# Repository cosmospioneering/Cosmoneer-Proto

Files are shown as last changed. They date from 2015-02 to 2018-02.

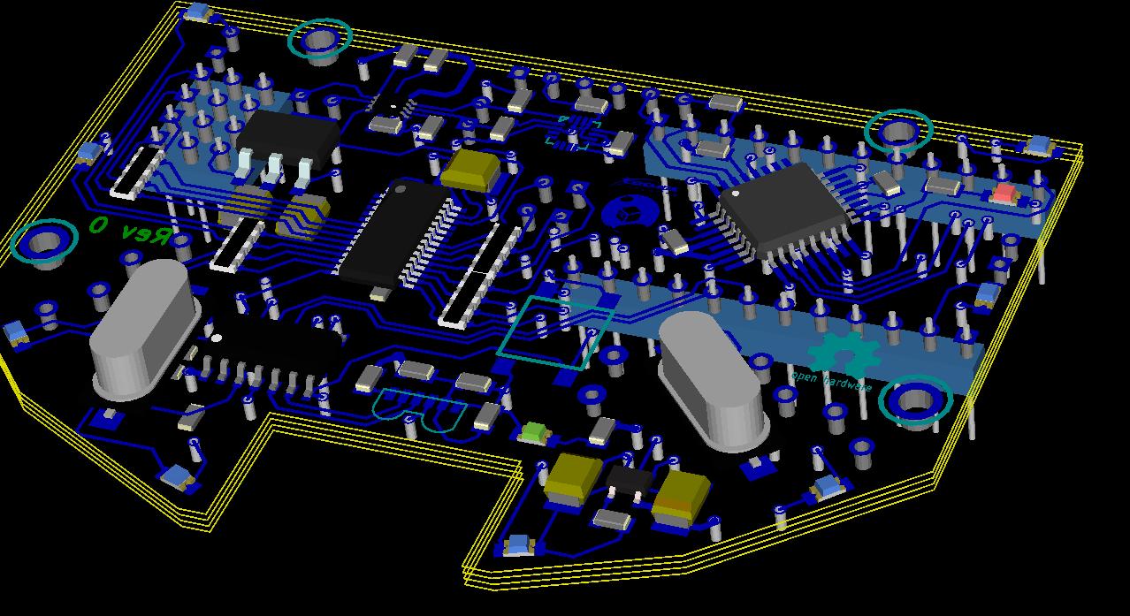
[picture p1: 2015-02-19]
CosmoneerJr_3D_Rev0.jpg

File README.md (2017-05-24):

#Cosmos Pioneering   -   Cosmoneer Proto#
==========================================

The Cosmoneer Proto is a single-degree of Freedom Spacecraft simulator.  This design is the main control board to manage the attitude in a single axis via PWM control through a server and gyro motor, commonly known as a Control Moment Gyro.

----------

# CONTENTS #

This repository contains source files for the Cosmoneer Proto.  Here is a table of contents for the repository.

- 3DModels: Rhino 3.0 models, with a sub folder containing Rhino output STL files
- Arduino: Arduino code in two folders, with additional required libraries contained in a separate zip file.
- Rev0-fab: Rev 0 PCB fabrication files (copper, mask, silk, drill, dwg)
- SpecSheets: Manufacturing spec sheets for components used on the Cosmoneer Proto circuit board
- fab: Rev 01 PCB fabrication files (copper, mask, silk, drill, dwg)
- boards: [KiCAD](http://www.kicad-pcb.org/display/KICAD/KiCad+EDA+Software+Suite) PCB board files (CosmoneerProto, SuperBurst & Serial IrDa)

# LICENSE #

*This project is open source hardware as defined by the* [Open Source Hardware (OSHW) Definition 1.0](http://freedomdefined.org/OSHW)
- Documentation under the following license:  [Creative Commons Attribution-ShareAlike 4.0 Unported License](http://creativecommons.org/licenses/by-sa/4.0/)
- Source code is under the following license:  [GNU General Public License, version 3 (GPL-3.0)](https://opensource.org/licenses/GPL-3.0)

[][1] [][3] [][5]

[1]: http://creativecommons.org/licenses/by-sa/4.0/
[2]: http://i.creativecommons.org/l/by-sa/4.0/88x31.png (Creative Commons Attribution-ShareAlike 4.0 Unported License.)

[3]: http://freedomdefined.org/OSHW
[4]: http://www.oshwa.org/wp-content/uploads/2014/03/oshw-logo-antipixel.png

[5]: https://opensource.org/licenses/GPL-3.0
[6]: https://www.gnu.org/graphics/gplv3-88x31.png

----------

# Disclaimer #

THE CONTENT OF THIS FOLDER IS PROVIDED "AS IS" AND "WITH ALL FAULTS". Cosmos Pioneering DISCLAIMS ALL OTHER WARRANTIES, EXPRESS OR IMPLIED, REGARDING PRODUCTS, INCLUDING BUT NOT LIMITED TO, ANY IMPLIED WARRANTIES OF MERCHANTABILITY OR FITNESS FOR A PARTICULAR PURPOSE.

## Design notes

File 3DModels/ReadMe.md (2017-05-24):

*3D Model File Notes*

1. The files are provided are used with Rhino 3.0.
  1. UOM is in millimeters
  2. STL files are generated using the following Rhino settings
    1. ?
    2. ?
2. STL files are provided for final component production.

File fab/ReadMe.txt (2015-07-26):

1> Copper weight & Layer thickness & material
     1oz copper.  Board thickness is .062"., FR4
 
2> Hole size tolerance and plating
     All holes are plated through, +/-003"(+/-0.08mm)

3> Soldermask tolerance & color
     .003"(0.075mm)  Color, blue
 
4> Plating & Leveling
     Hot Air Solder Level
 
5> Silkscreen side & color
     Top & Bottom silkscreen.  Color, White.
 
6> Dimensional size & tolerance
     70mm(2.756")  X  50mm(1.968"),  +/- 0.012"(0.3mm)
     Max radius on inside pcb corners is .070"
 
7> Electrical testing
     Electrical testing is not required

8> Inner layer isolated pads
    Isolated pads may be removed from inner layers.
 
9> Datecode & Mfg Marking
    Date Code and Mfg Code are not required.

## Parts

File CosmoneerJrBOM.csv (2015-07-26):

Id | Designator | Package | Quantity | Designation | Supplier and ref
1 | U3 | vishay_TFBS4711 | 1 | TFBS4711
2 | U1 | TQFP32 | 1 | ATMEGA328P-AU
3 | SW1 | SW_PUSH_SMD | 1 | SW_PUSH_SMALL
4 | U7 | SOT23-5 | 1 | MIC5205
5 | U8 | SOT223 | 1 | AMS1117
6 | U2 | so-14 | 1 | MCP2120-SL
7 | C15,C12,C11,C10,C17,C16,C3,C5 | SM0805 | 8 | 0.1uf
8 | R24,R22,R23,R20,R21,R7 | SM0805 | 6 | 10K
9 | R19,R18 | SM0805 | 2 | 1K
10 | C7,C14,C13,C6 | SM0805 | 4 | 22pf
11 | C8,C2,C4 | SM0805 | 3 | 4.7uf
12 | C9 | SM0805 | 1 | 0.22uf
13 | R17 | SM0805 | 1 | 0 Ohm
14 | R16 | SM0805 | 1 | 47 Ohm
15 | P1 | SIL-6 | 1 | .1in Header
16 | P2,P5,P4,P6 | SIL-2 | 4 | Header
17 | J17,J18 | SIL-12 | 2 | Header
18 | JP1,JP3,JP2,JP4,JP5 | S_JUMPER_3 | 5 | JUMPER3
19 | R25,R28 | r_CN2A4 | 2 | 220 Ohm
20 | R26,R27 | r_CN2A4 | 2 | 330 Ohm
21 | X2 | Q_49U3HMS | 1 | 16.000Mhz
22 | X1 | Q_49U3HMS | 1 | 7.3728Mhz
23 | J5,J1,J9,J13 | PIN_ARRAY_3X1 | 4 | Header
24 | PZ1 | piezo_spkr | 1 | PIEZO Speaker
25 | U4 | pca9306dcu | 1 | PCA9306
26 | D10,D9,D7,D8,D4,D6,D1,D2,D3,D5 | LED-0805 | 10 | LED
27 | U5 | HMC5883L_bigpads | 1 | HMC5883
28 | P3 | con-jst2-SM04B-SRSS-TB | 1 | SM04B-SRSS-TB
29 | C18,C1,C20,C21,C19 | c_tant_B | 5 | 10uf
30 | U9 | PCA9685 | 1 | PCA9685
31 | P7,P8 | SIL-2 | 2 | CONN_2
32 | 1PIN,1PIN,1PIN,1PIN | Mhole | 4 | P***
33 | PressFitPCB,PressFitPCB | PressFitPCB | 2 | VAL**
34 | G*** | Logo_silk_OSHW_6x6mm | 1 | LOGO
35 | VAL | LOGO | 1 | REF

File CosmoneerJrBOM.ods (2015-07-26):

Id | Designator | Package | Designation | Quantity | Supplier and ref
1 | U1 | TQFP32 | ATMEGA328P-AU | 1
2 | U2 | so-14 | MCP2120-SL | 1
3 | U3 | vishay_TFBS4711 | TFBS4711 | 1
4 | U4 | pca9306dcu | PCA9306 | 1
5 | U5 | HMC5883L_bigpads | HMC5883 | 1
6 | U7 | SOT23-5 | MIC5205 | 1
7 | U8 | SOT223 | AMS1117 | 1
8 | U9 | PCA9685 | PCA9685 | 1
9 | X1 | Q_49U3HMS | 7.3728Mhz | 1
10 | X2 | Q_49U3HMS | 16.000Mhz | 1
11 | SW1 | SW_PUSH_SMD | SW_PUSH_SMALL | 1
12 | PZ1 | piezo_spkr | PIEZO Speaker | 1
13 | D10,D9,D7,D8,D4,D6,D1,D2,D3,D5 | LED-0805 | LED | 10
14 | C15,C12,C11,C10,C17,C16,C3,C5 | SM0805 | 0.1uf | 8
15 | C9 | SM0805 | 0.22uf | 1
16 | C8,C2,C4 | SM0805 | 4.7uf | 3
17 | C18,C1,C20,C21,C19 | c_tant_B | 10uf | 5
18 | C7,C14,C13,C6 | SM0805 | 22pf | 4
19 | R17 | SM0805 | 0 Ohm | 1
20 | R16 | SM0805 | 47 Ohm | 1
21 | R19,R18 | SM0805 | 1K | 2
22 | R24,R22,R23,R20,R21,R7 | SM0805 | 10K | 6
23 | R26,R27 | r_CN2A4 | 330 Ohm | 2
24 | R25,R28 | r_CN2A4 | 220 Ohm | 2
25 | P1 | SIL-6 | .1in Header | 1
26 | P2,P5,P4,P6 | SIL-2 | Header | 4
27 | P7,P8 | SIL-2 | CONN_2 | 2
28 | J5,J1,J9,J13 | SIL-3 | Header | 4
29 | J17,J18 | SIL-12 | Header | 2
30 | P3 | con-jst2-SM04B-SRSS-TB | SM04B-SRSS-TB | 1
31 | PressFitPCB,PressFitPCB | PressFitPCB | VAL** | 2

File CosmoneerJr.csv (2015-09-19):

Id | Designator | Package | Quantity | Designation | Supplier and ref
1 | U3 | vishay_TFBS4711 | 1 | TFBS4711
2 | U1 | TQFP32 | 1 | ATMEGA328P-AU
3 | U7 | SOT23-5 | 1 | MIC5205
4 | U2 | so-14 | 1 | MCP2120-SL
5 | C15 | C12 | C17 | C16 | C3 | C5 | SM0805 | 6 | 0.1uf
6 | R24 | R20 | R21 | R7 | SM0805 | 4 | 10K
7 | R19 | R18 | SM0805 | 2 | 1K
8 | C7 | C6 | SM0805 | 2 | 27pf
9 | C2 | C4 | SM0805 | 2 | 4.7uf
10 | C14 | C13 | SM0805 | 2 | 15pf
11 | R17 | SM0805 | 1 | 0 Ohm
12 | R16 | SM0805 | 1 | 47 Ohm
13 | P1 | SIL-6 | 1 | .1 Header
14 | P2 | P4 | P6 | SIL-2 | 3 | Header
15 | J17 | J18 | SIL-12 | 2 | Header
16 | JP1 | JP3 | JP2 | JP4 | JP5 | S_JUMPER_3 | 5 | JUMPER3
17 | X2 | Q_49U3HMS | 1 | 16.000Mhz
18 | X1 | Q_49U3HMS | 1 | 7.3728Mhz
19 | J5 | J1 | J9 | J13 | PIN_ARRAY_3X1 | 4 | Header
20 | PZ1 | piezo_spkr | 1 | PIEZO Speaker
21 | D10 | D9 | D7 | D8 | D4 | D6 | D1 | D2 | D3 | D5 | LED-0805 | 10 | LED
22 | P3 | con-jst2-SM04B-SRSS-TB | 1 | SM04B-SRSS-TB
23 | C18 | C1 | C21 | C19 | C20 | c_tant_B | 5 | 10uf
24 | U9 | PCA9685 | 1 | PCA9685
25 | P7 | P8 | SIL-2 | 2 | CONN_2
30 | R26 | R25 | R27 | R28 | r_cat16-4 | 4 | 330 Ohm
31 | SW1 | smd_push2 | 1 | SW_PUSH_SMALL
32 | GY-271 | GY-271 | 1 | U10
33 | U8 | SOT223 | 1 | AMS1117
34 | F1 | SM1812 | 1 | FUSE
35 | D11 | DO-214AC(SMA) | 1 | 1N4001

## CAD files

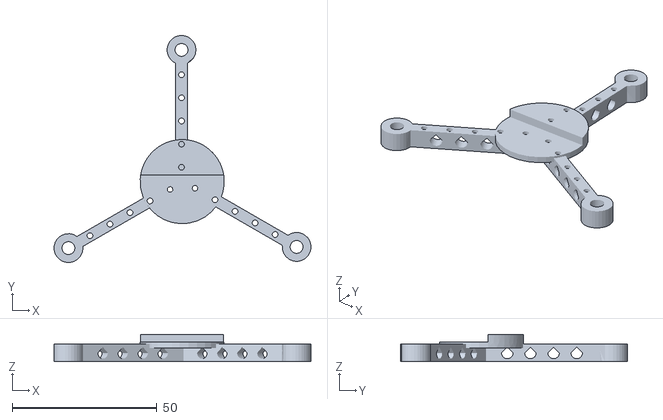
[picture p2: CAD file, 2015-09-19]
3DModels/3DPrintFiles/BalancerMain.stl
88.9 x 78.5 x 9.40

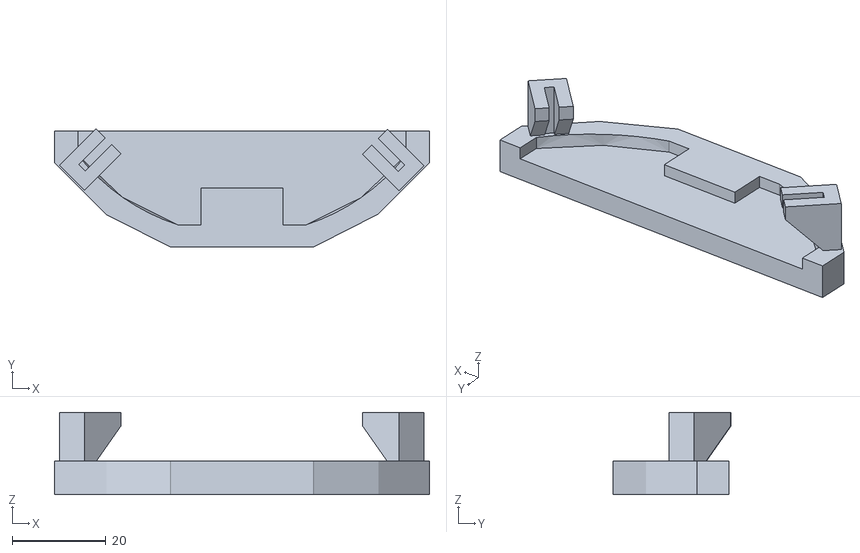
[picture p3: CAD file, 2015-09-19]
3DModels/3DPrintFiles/SupportJig_v2.stl
80.0 x 25.2 x 17.5

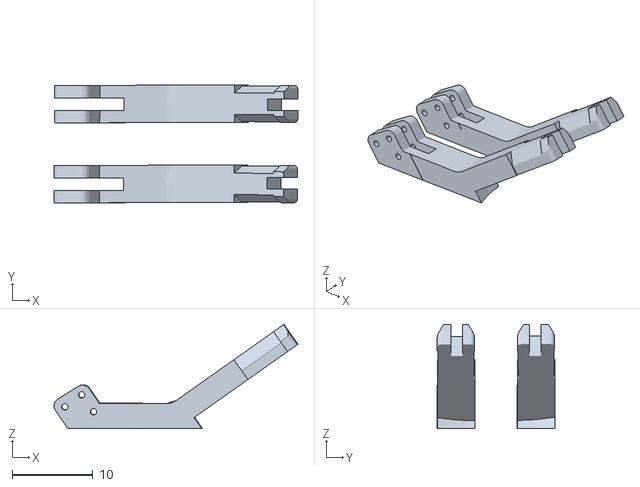
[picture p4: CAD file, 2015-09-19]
3DModels/3DPrintFiles/Legs_v2.stl
30.2 x 14.6 x 12.9

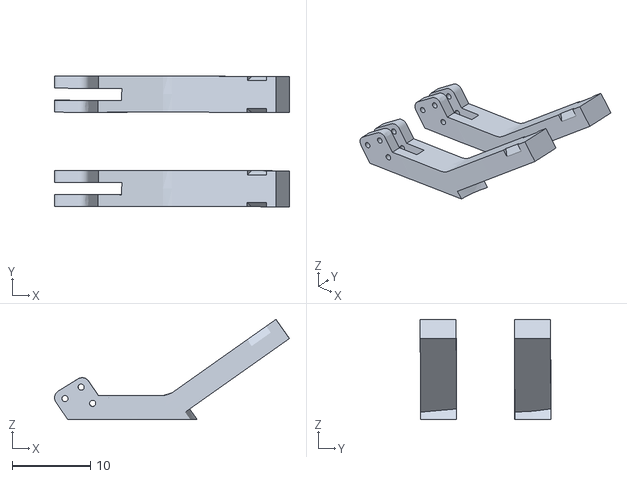
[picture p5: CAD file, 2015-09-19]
3DModels/3DPrintFiles/Legs.stl
30.1 x 16.8 x 12.9

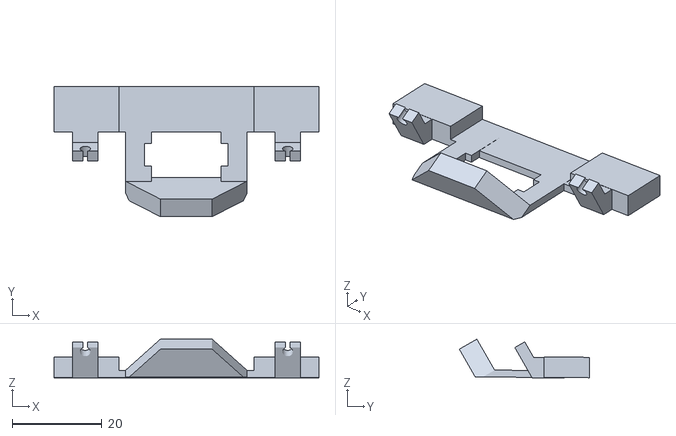
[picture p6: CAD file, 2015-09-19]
3DModels/3DPrintFiles/Evo_RearSupport_v3.stl
58.9 x 29.0 x 8.61

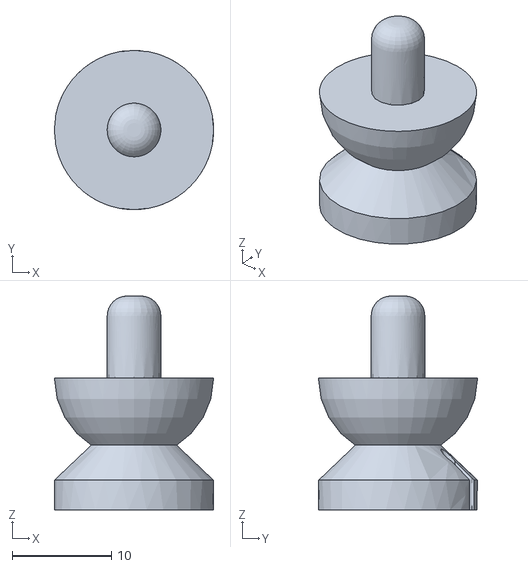
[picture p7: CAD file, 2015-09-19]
3DModels/3DPrintFiles/Spool_v6.stl
16.0 x 16.0 x 21.5

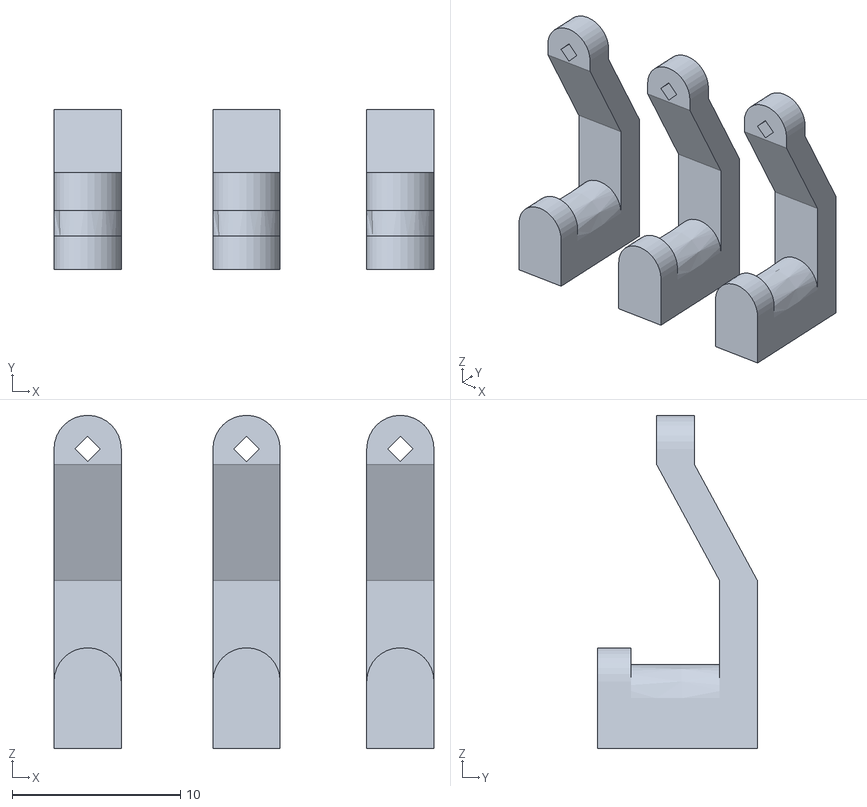
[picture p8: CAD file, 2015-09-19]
3DModels/3DPrintFiles/HangersX3_v2.stl
22.6 x 9.50 x 19.8

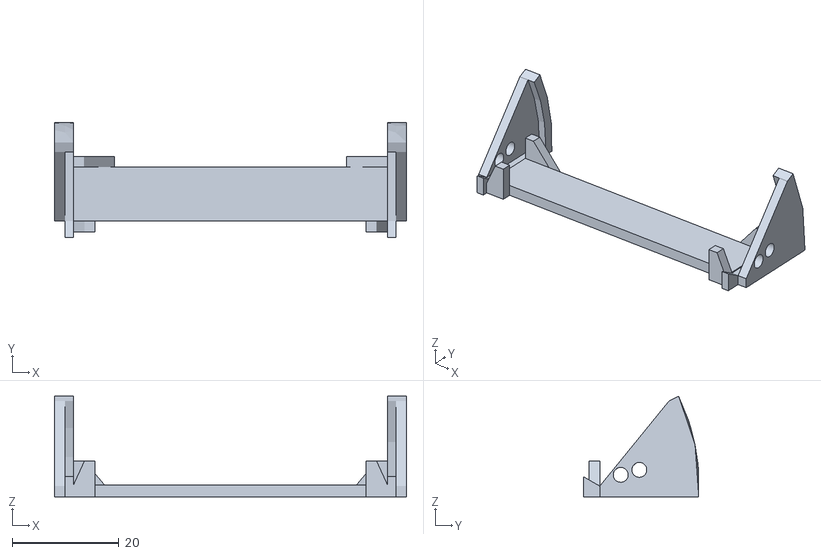
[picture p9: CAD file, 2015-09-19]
3DModels/3DPrintFiles/TopJig_v2.stl
66.0 x 21.7 x 18.9

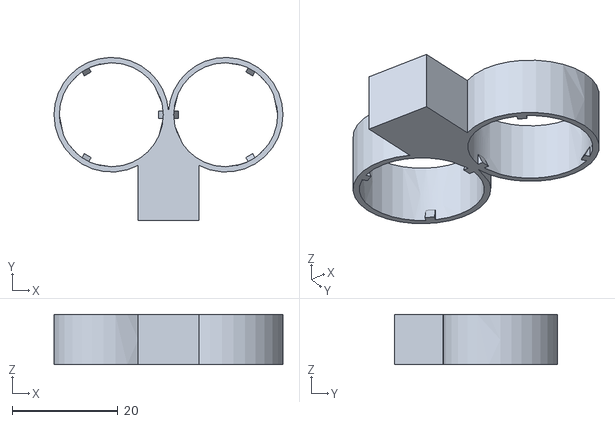
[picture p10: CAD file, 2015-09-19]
3DModels/3DPrintFiles/Counterweight_v1.stl
43.4 x 30.9 x 9.50

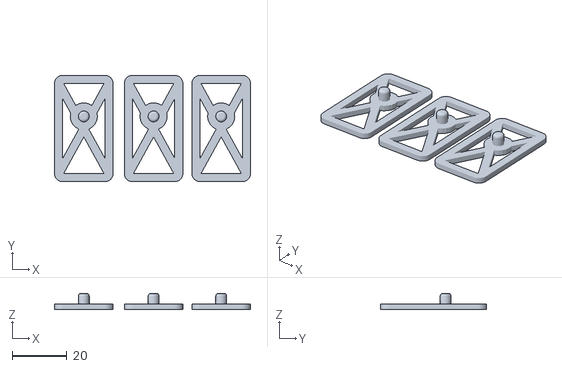
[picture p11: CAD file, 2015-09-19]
3DModels/3DPrintFiles/BalancerFeet.stl
71.9 x 39.0 x 6.00

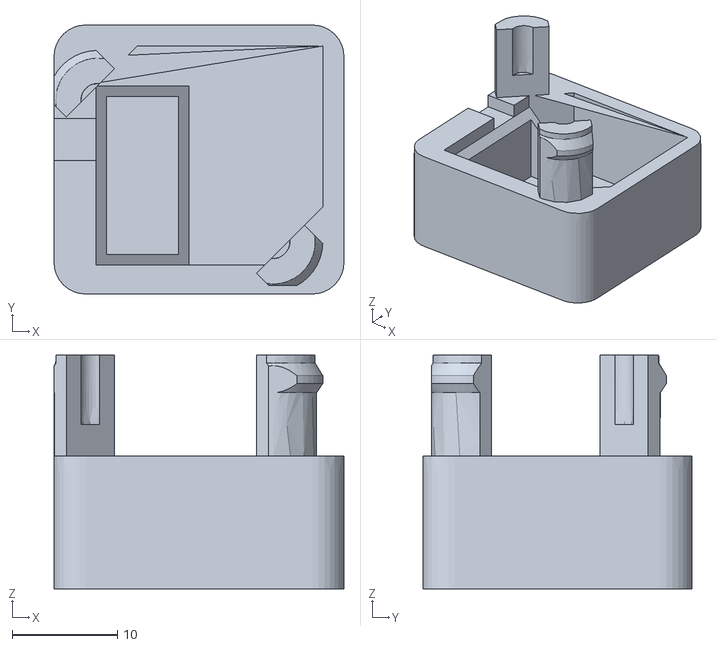
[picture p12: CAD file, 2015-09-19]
3DModels/3DPrintFiles/ChargeCover_v4.stl
27.5 x 25.6 x 22.2

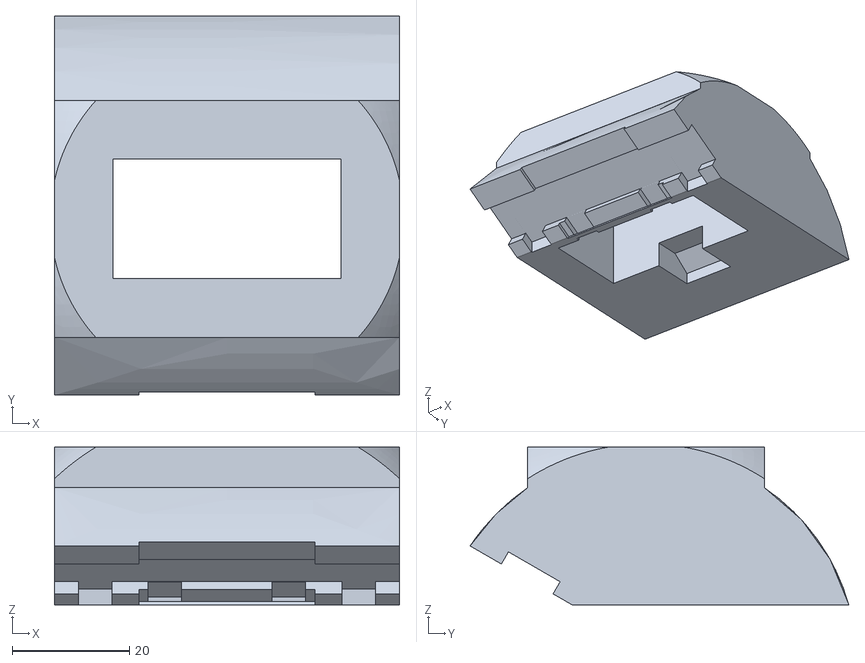
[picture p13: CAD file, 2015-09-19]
3DModels/3DPrintFiles/SeatingTool.stl
58.9 x 64.7 x 26.9

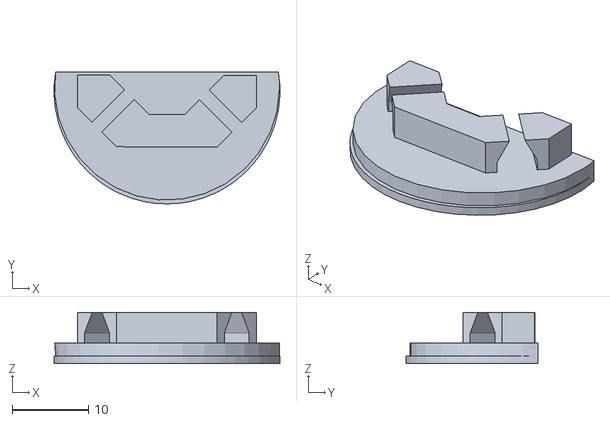
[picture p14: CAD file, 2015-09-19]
3DModels/3DPrintFiles/CoilPlate_v2.stl
29.6 x 17.3 x 6.70

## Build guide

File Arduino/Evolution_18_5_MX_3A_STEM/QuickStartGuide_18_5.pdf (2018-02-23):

## Your Cosmoneer is running open source test code!

To modify our code,
download and install
Arduino v1.6.10. Then,
install the library zip files in the project subfolder.

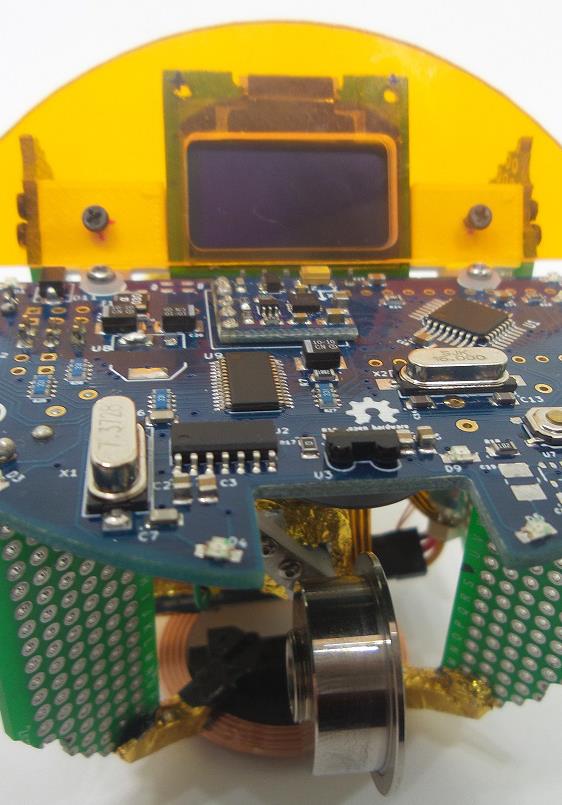
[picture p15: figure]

Your loaded version is:
Evolution_18_5_MX-3A_STEM

https://git.io/vA2jV

Replacement 3D parts:

https://www.thingiverse.
com/thing:2159548 (https://www.thingiverse.com/thing:2159548)

https://www.thingiverse.
com/thing:2154587 (https://www.thingiverse.com/thing:2154587)

You’ll find plenty of our Cosmoneer resources and useful information by visiting any one of the links below.

## Manuals & Documentation

http://cosmospioneering.com/manuals-and-docs/ (http://cosmospioneering.com/manuals-and-docs/)

## Cosmoneer User Community

http://cosmospioneering.com/community/

## GitHub Repository

https://github.com/cosmospioneering/Cosmoneer-Proto (https://github.com/cosmospioneering/Cosmoneer-Proto)

## Detailed Assembly Guide:

http://www.instructables.com/id/Cosmoneer-Proto/ (http://www.instructables.com/id/Cosmoneer-Proto/)

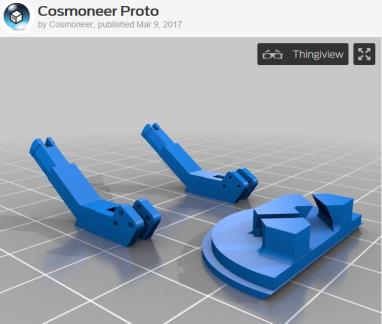
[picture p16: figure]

## Contact Us

PO Box 591 Damascus, MD 20872 240-200-4189
Cosmoneer@cosmospioneering.com http://www.cosmospioneering.com
- @Cosmoneer
- facebook.com/cosmos.pioneering

## Quick Start Guide

Congratulations on your purchase!

Your adventure in space
exploration begins here. Please take a moment to familiarize yourself with your personal desktop spacecraft.

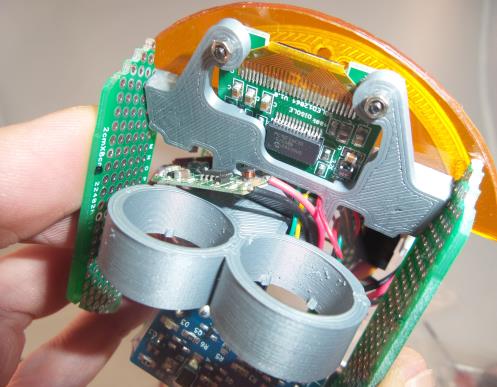
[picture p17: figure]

## Unboxing & Setup

Before removing your Cosmoneer from the box, please ensure you have a location available where your Cosmoneer will be level, safe & sound, and have an outlet within 3ft.

Find a smooth surface where you can lay out the parts. Carefully pull the Cosmoneer and its support
components from the box and place them on your surface.

Pull the hook and spool
from the Ziploc bag and
insert the spool into the
top of the hanger. Thread the string so it spills over the
edge towards the
center of the coil.

Place the unit in your
chosen location and
connect the power. It
is normal for the coil to
get warm during use.

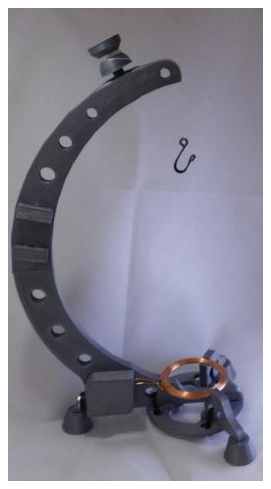
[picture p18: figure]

We recommend you use an adhesive or no-slip surface to prevent damage to your Cosmoneer from a fall during normal operation.

With the Cosmoneer in hand, place an equal number of the provided pennies into each of the wells in the rear of the Cosmoneer (shown above.)

## To sphere or not to sphere?

Your Cosmoneer can operate from within the 100mm sphere, or it can run while exposed to the harsh environment you have chosen. The sphere will smooth the Cosmoneers’ operations a bit, due to added mass.

If your Cosmoneer is experiencing high rotational speed, use the sphere. If you need more power, remove the sphere and suspend from the internal arch in front of the display which will allow you to reduce the coil airgap.

Using the sphere
Correctly placing the Cosmoneer into the sphere has been simplified via rubber guides. To start, grasp the sphere half containing the guides, open side facing up.

The guide opposite the hanger loop is where the coil of the Cosmoneer will sit. With the Cosmoneer in your other hand, lay it on its back and align the coil hanger as shown. Be sure to align the
dash panel
against the guides
at the opposite
end of the sphere.

With everything

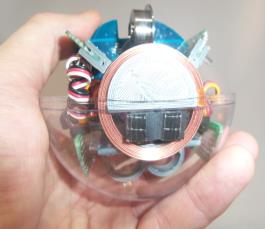
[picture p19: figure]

aligned, join the
sphere halves
together, making
sure the pennies
don’t fall out of
the holder.

## Launch!

To launch, simply place the craft onto the hook and adjust the spool so the craft is suspended just above the coil. Your Cosmoneer will power up in about ten seconds. Have fun!

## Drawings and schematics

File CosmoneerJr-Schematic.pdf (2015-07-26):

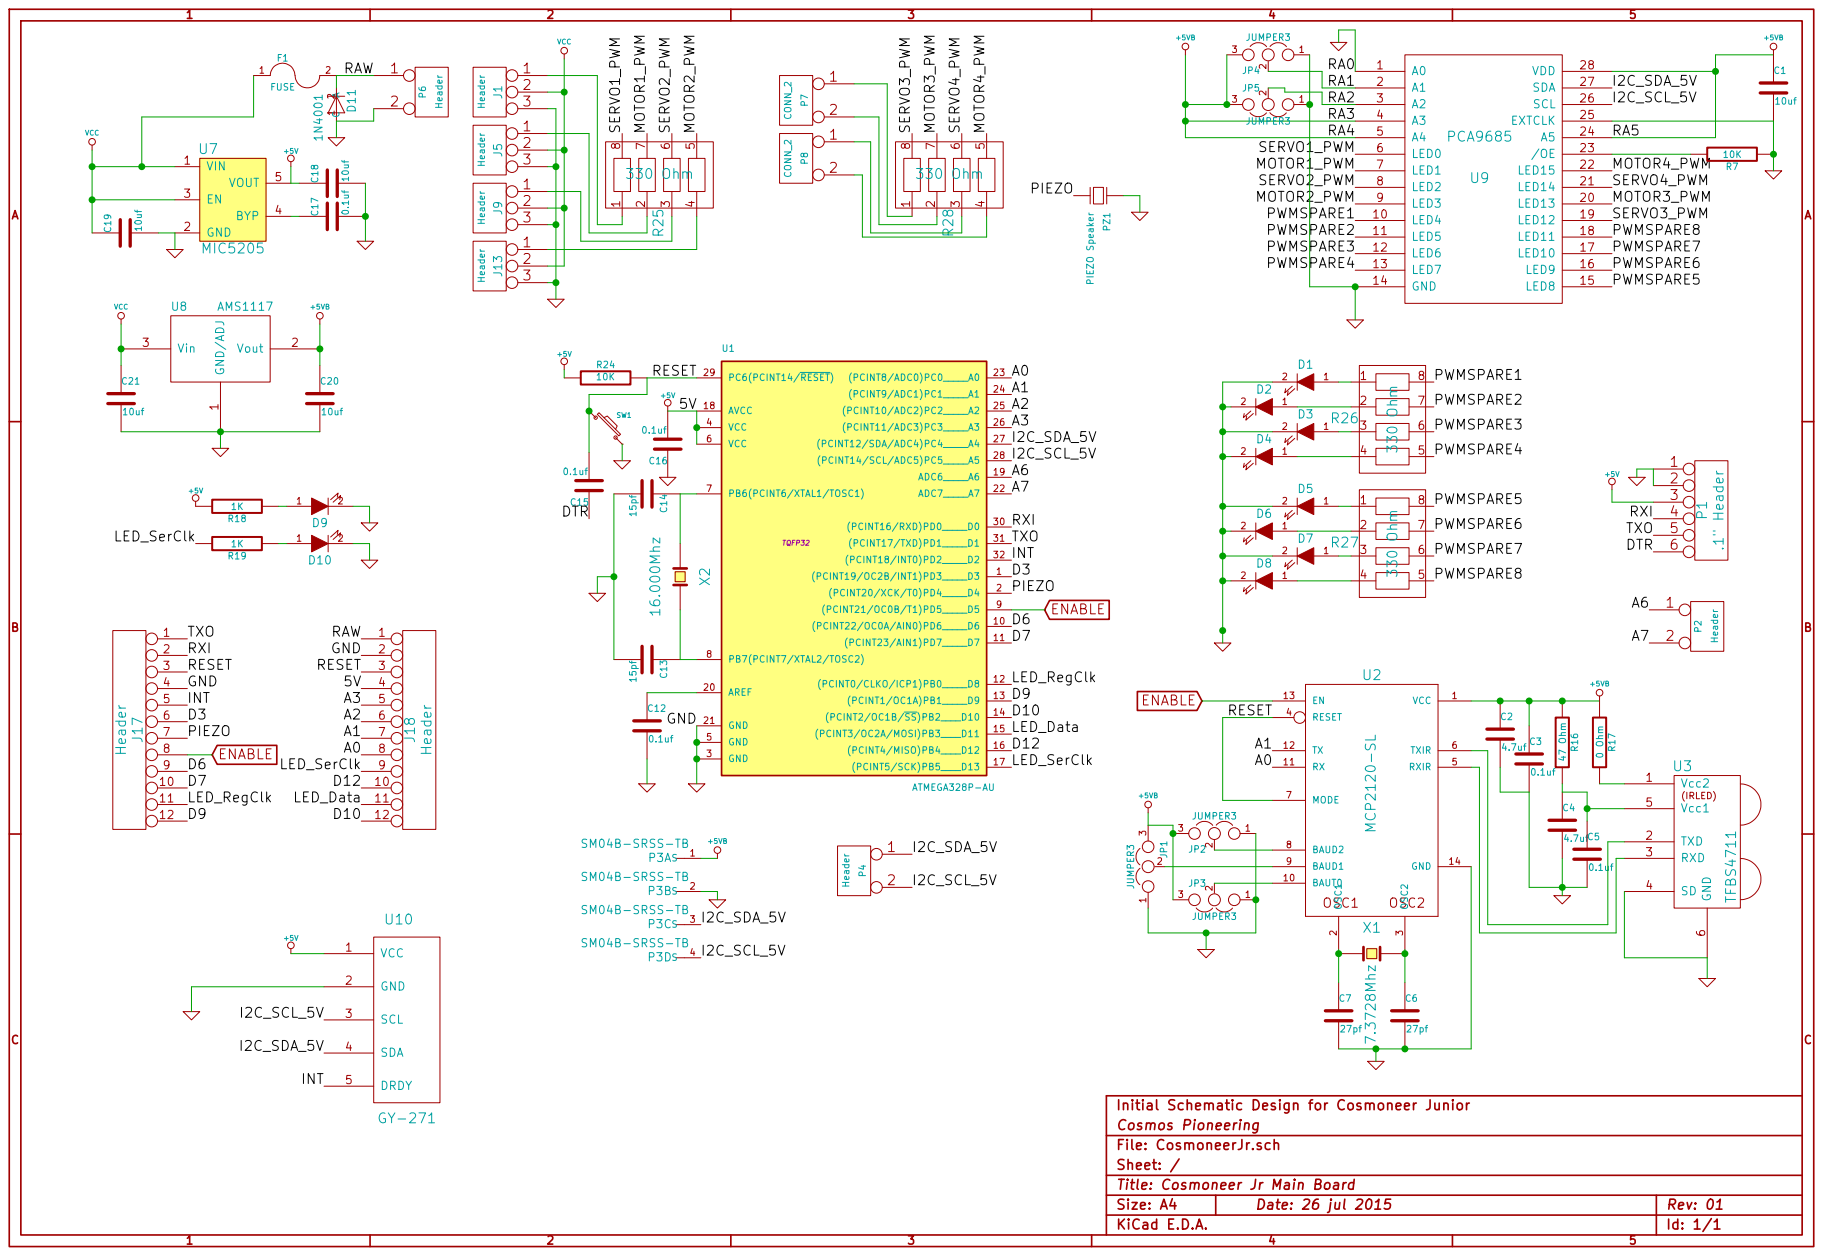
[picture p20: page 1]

3 RESET 4 RXIR 5 TXIR 6 MODE 7 BAUD2 8 BAUD1 9 BAUT0 10 RX 11 TX 12 EN 13 GND 14 U2MCP2120-SL ENABLE

Initial Schematic Design for Cosmoneer Junior
Id: 1/1 Title: Cosmoneer Jr Main Board File: CosmoneerJr.sch Sheet: / Cosmos Pioneering

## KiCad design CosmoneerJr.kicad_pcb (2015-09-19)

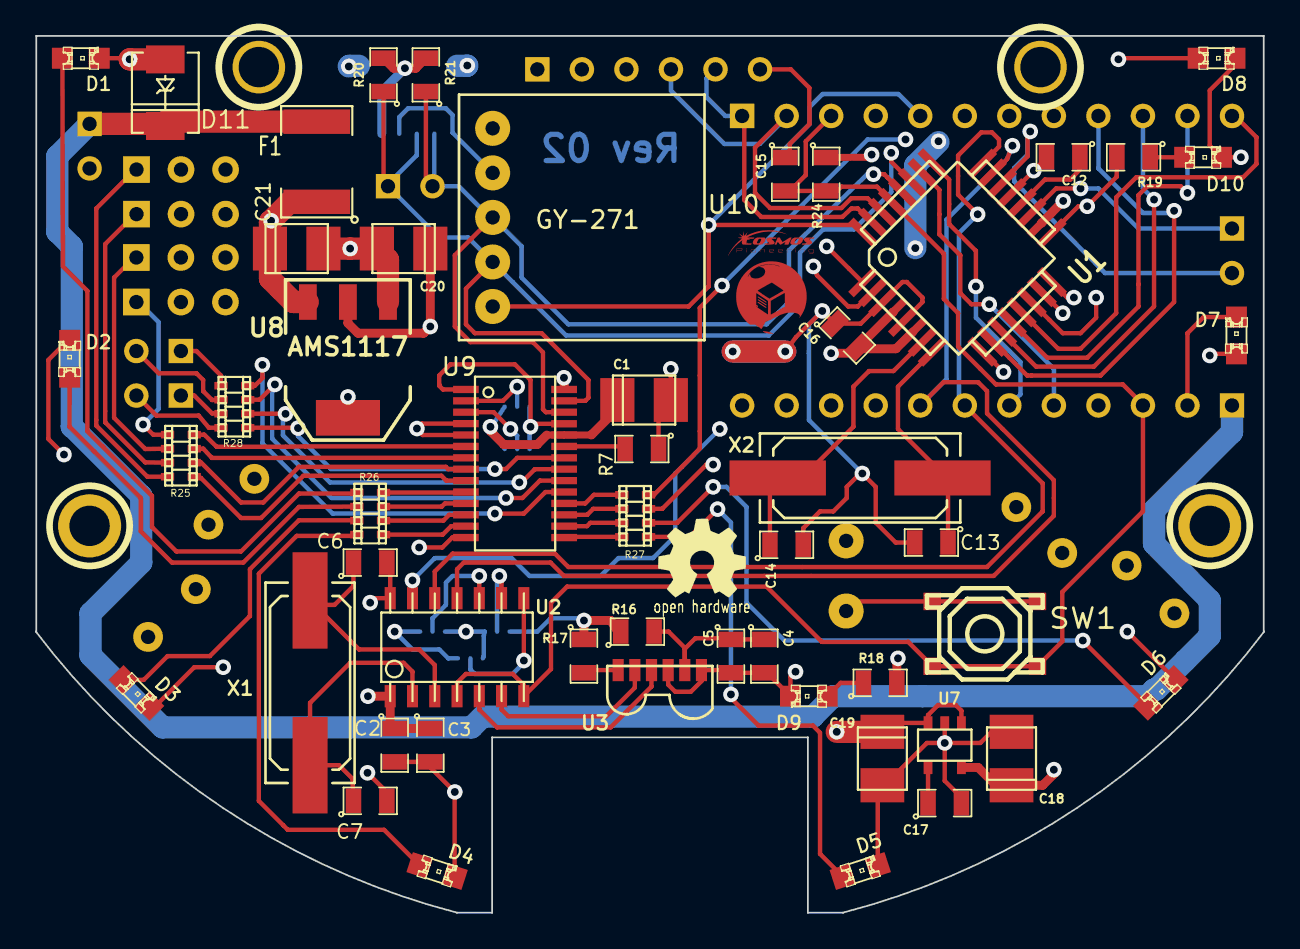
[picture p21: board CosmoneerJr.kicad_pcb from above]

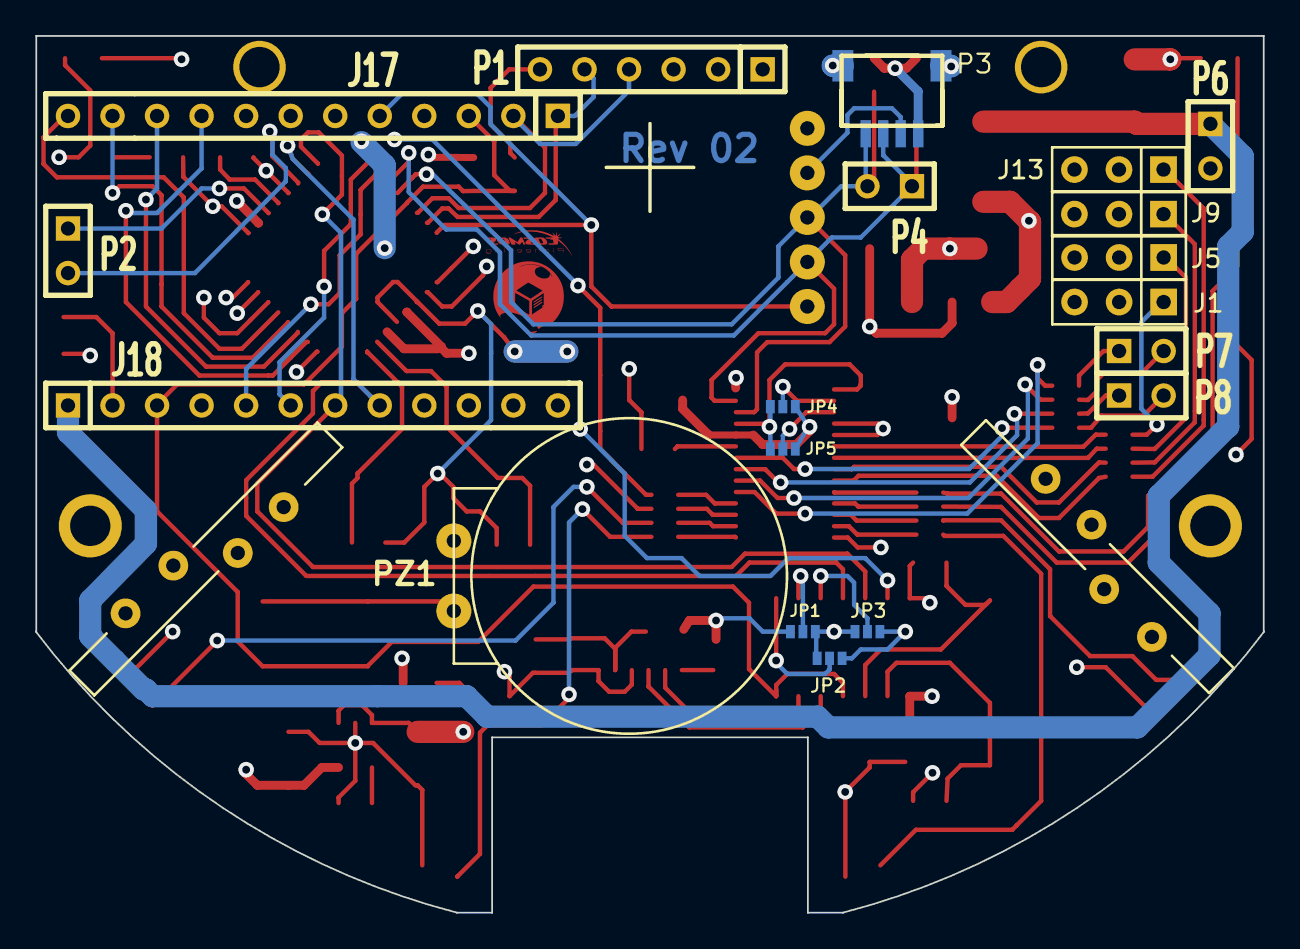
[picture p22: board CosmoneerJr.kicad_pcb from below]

Board: 4 copper layers, 70.0 x 50.0 mm, 77 parts (21 on the bottom side), 78 nets.

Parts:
1PIN, 1PIN#2, 1PIN#3, 1PIN#4: P***; Mhole
C1, C18, C19, C20, C21: 10uf; c_tant_B
C2, C4: 4.7uf; SM0805
C3, C5, C12, C15, C16, C17: 0.1uf; SM0805
C6, C7: 27pf; SM0805
C13, C14: 15pf; SM0805
D1, D2, D3, D4, D5, D6, D7, D8, D9, D10: LED; LED-0805
D11: 1N4001; DO-214AC(SMA)
F1: FUSE; SM1812
GY-271: U10; GY-271
J1, J5, J9, J13: Header; PIN_ARRAY_3X1
J17, J18: Header; SIL-12
JP1, JP2, JP3, JP4, JP5: JUMPER3; S_JUMPER_3
P1: .1" Header; SIL-6
P2, P4, P6: Header; SIL-2
P3: SM04B-SRSS-TB; con-jst2-SM04B-SRSS-TB
P7, P8: CONN_2; SIL-2
PZ1: PIEZO Speaker; piezo_spkr
PressFitPCB: VAL**; PressFitPCB
PressFitPCB#2: VAL**; PressFitPCB
R7, R20, R21, R24: 10K; SM0805
R16: 47 Ohm; SM0805
R17: 0 Ohm; SM0805
R18, R19: 1K; SM0805
R25, R26, R27, R28: 330 Ohm; r_cat16-4
SW1: SW_PUSH_SMALL; smd_push2
U1: ATMEGA328P-AU; TQFP32
U2: MCP2120-SL; so-14
U3: TFBS4711; vishay_TFBS4711
U7: MIC5205; SOT23-5
U8: AMS1117; SOT223
U9: PCA9685
VAL: REF; LOGO
X1: 7.3728Mhz; Q_49U3HMS
X2: 16.000Mhz; Q_49U3HMS

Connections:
+5V: C1.1, C2.1, C3.1, C16.2, C18.1, C20.1, GY-271.1, J18.4, JP1.3, JP2.3, JP3.3, JP4.3, JP5.3, P1.3, P3.1, R16.1, R17.1, R18.2, R20.2, R21.2, R24.1, U1.4, U1.6, U1.18, U2.1, U7.5, U8.2, U8.4, U9.4, U9.5, U9.24, U9.28
/A0: J18.8, U1.23, U2.11
/A1: J18.7, U1.24, U2.12
/A2: J18.6, U1.25
/A3: J18.5, U1.26
/A6: P2.1, U1.19
/A7: P2.2, U1.22
/D3: J17.6, U1.1
/D6: J17.9, U1.10
/D7: J17.10, U1.11
/D9: J17.12, U1.13
/D10: J18.12, U1.14
/D12: J18.10, U1.16
/DTR: C15.1, P1.6
/I2C_SCL_5V: GY-271.3, P3.4, P4.2, R21.1, U1.28, U9.26
/I2C_SDA_5V: GY-271.4, P3.3, P4.1, R20.1, U1.27, U9.27
/INT: GY-271.5, J17.5, U1.32
/LED_Data: J18.11, U1.15
/LED_RegClk: J17.11, U1.12
/LED_SerClk: J18.9, R19.2, U1.17
/MOTOR1_PWM: R25.7, U9.7
/MOTOR2_PWM: R25.5, U9.9
/MOTOR3_PWM: R28.7, U9.20
/MOTOR4_PWM: R28.5, U9.22
/PIEZO: J17.7, PZ1.2, U1.2
/PWMSPARE1: R26.8, U9.10
/PWMSPARE2: R26.7, U9.11
/PWMSPARE3: R26.6, U9.12
/PWMSPARE4: R26.5, U9.13
/PWMSPARE5: R27.8, U9.15
/PWMSPARE6: R27.7, U9.16
/PWMSPARE7: R27.6, U9.17
/PWMSPARE8: R27.5, U9.18
/RA1: JP4.2, U9.2
/RA2: JP5.2, U9.3
/RAW: D11.2, F1.2, J18.1, P6.1
/RESET: C15.2, J17.3, J18.3, R24.2, SW1.1, SW1.4, U1.29, U2.4, U2.7
/RXI: J17.2, P1.4, U1.30
/SERVO1_PWM: R25.8, U9.6
/SERVO2_PWM: R25.6, U9.8
/SERVO3_PWM: R28.8, U9.19
/SERVO4_PWM: R28.6, U9.21
/TXO: J17.1, P1.5, U1.31
ENABLE: J17.8, U1.9, U2.13
GND: 1PIN#3.1, C1.2, C2.2, C3.2, C4.2, C5.2, C6.2, C7.2, C12.2, C13.2, C14.2, C16.1, C17.2, C18.2, C19.2, C20.2, C21.2, D1.2, D2.2, D3.2, D4.2, D5.2, D6.2, D7.2, D8.2, D9.2, D10.2, D11.1, GY-271.2, J1.3, J5.3, J9.3, J13.3, J17.4, J18.2, JP1.1, JP2.1, JP3.1, JP4.1, JP5.1, P1.1, P1.2, P3.2, P3.FIT@, P6.2, PZ1.1, R7.1, SW1.2, SW1.3, U1.3, U1.5, U1.21, U2.14, U3.4, U3.6, U7.2, U8.1, U9.1, U9.14, U9.25
unnamed: JP3.2, U2.10
unnamed: C12.1, U1.20
unnamed: U2.5, U3.3
unnamed: U2.6, U3.2
unnamed: C4.1, C5.1, R16.2, U3.5
unnamed: JP2.2, U2.8
unnamed: JP1.2, U2.9
unnamed: D10.1, R19.1
unnamed: C17.1, U7.4
unnamed: D9.1, R18.1
unnamed: C14.1, U1.7, X2.1
unnamed: C13.1, U1.8, X2.2
unnamed: R7.2, U9.23
unnamed: P8.1, R28.3
unnamed: P8.2, R28.4
unnamed: P7.1, R28.1
unnamed: P7.2, R28.2
unnamed: J13.1, R25.4
unnamed: J1.1, R25.1
unnamed: J5.1, R25.2
unnamed: J9.1, R25.3
unnamed: D6.1, R27.2
unnamed: D1.1, R26.1
unnamed: D2.1, R26.2
unnamed: D3.1, R26.3
unnamed: D4.1, R26.4
unnamed: D5.1, R27.1
unnamed: D7.1, R27.3
unnamed: D8.1, R27.4
unnamed: R17.2, U3.1
unnamed: C7.1, U2.2, X1.1
unnamed: C6.1, U2.3, X1.2
VCC: C19.1, C21.1, F1.1, J1.2, J5.2, J9.2, J13.2, U7.1, U7.3, U8.3

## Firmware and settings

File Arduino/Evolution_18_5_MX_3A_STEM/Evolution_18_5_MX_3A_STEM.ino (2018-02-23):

#include <MPU6050_6Axis_MotionApps20.h>


//----------------------------------------------
//    Wire Library   - I2C Bus Communications
//----------------------------------------------
#include <Wire.h>
//#include <i2cdetect.h>
//    This is required for...
//    Magnetometer
//    PWM Controller  
//    OLED Display (optional)
//
//
//Thanks, Adafruit for the awesome Servo Driver Library!
#include <Adafruit_PWMServoDriver.h>
//
//OLED Display interface
#define _Digole_Serial_I2C_  //To tell compiler compile the special communication only, 
#include <DigoleSerial.h>
//
//Compass interface & calibration code
#include "compass.h"
#include <MPU6050.h>


#include <string.h>



//----------------------------------------------
//    SoftSerial Library   - For Serial IrDa
//----------------------------------------------
#include <SoftwareSerial.h>



//----------------------------------------------
//    EEProm Library   - For Compass Cal Vals
//----------------------------------------------
#include <EEPROM.h>



//This is what is required for the timer event support
//----------------------------------------------
//    Timer Library   - Timed Events
//----------------------------------------------
#include "Timer.h"



#include "I2Cdev.h"
// class default I2C address is 0x68
// specific I2C addresses may be passed as a parameter here
// AD0 low = 0x68 (default for SparkFun breakout and InvenSense evaluation board)
// AD0 high = 0x69
MPU6050 mpu;




const uint8_t startscreenIV[1024] PROGMEM={
0,0,0,0,0,0,0,0,0,0,0,0,0,0,0,0
,0,0,0,0,0,0,0,0,0,0,0,0,0,0,0,0
,0,0,0,0,0,0,0,0,0,0,0,0,0,0,0,0
,0,0,0,0,0,0,0,0,0,0,0,0,0,0,0,0
,0,0,0,0,0,0,0,0,0,0,0,0,0,0,0,0
,0,0,0,0,0,0,0,0,0,0,0,0,0,0,0,0
,0,0,0,0,0,0,0,0,0,0,0,0,0,0,0,0
,0,0,0,0,0,0,0,0,0,0,0,0,0,0,0,0
,0,0,0,0,0,0,0,0,0,0,0,0,0,0,0,0
,0,0,0,0,0,0,0,0,0,0,0,0,0,0,0,0
,0,0,0,0,0,0,0,0,0,0,0,0,0,0,0,0
,0,0,0,0,0,0,0,0,0,0,0,0,0,0,0,0
,0,0,0,0,0,0,0,0,0,0,0,0,0,0,0,0
,0,0,0,0,0,0,0,0,0,0,0,0,0,0,0,0
,0,0,0,0,0,0,0,0,0,0,0,0,0,0,0,0
,0,0,0,0,0,0,0,0,0,0,0,0,0,0,0,0
,255,0,0,0,0,0,0,0,0,0,0,0,0,0,0,0
,128,0,0,0,0,0,0,0,0,0,0,0,0,0,0,0
,128,2,2,4,0,16,63,128,127,0,128,128,126,1,0,1
,255,2,2,4,0,16,0,64,0,128,128,128,195,1,0,1
,129,2,2,4,0,16,31,224,63,192,128,128,129,1,0,1
,129,2,2,4,0,16,48,32,96,64,128,128,129,1,1,255
,129,2,2,4,0,48,32,32,64,64,128,128,129,1,3,1
,255,3,252,4,15,224,63,192,127,128,255,0,255,1,2,1
,0,0,0,0,0,0,0,0,0,0,0,0,0,0,2,1
,0,0,0,4,0,0,0,0,0,0,0,0,0,1,3,255
,0,0,0,0,0,0,0,0,0,0,0,0,0,0,0,0
,0,0,0,0,0,0,0,0,0,0,0,0,0,0,0,0
,0,0,0,0,0,0,0,0,0,0,0,0,0,0,0,0
,0,0,0,0,0,0,0,0,0,0,0,0,0,0,0,0
,0,0,0,0,0,0,0,0,0,0,0,0,0,0,0,0
,15,255,248,255,255,15,248,240,51,255,254,63,255,227,255,252
,31,255,251,255,255,159,243,248,119,255,254,255,255,243,255,254
,31,248,3,252,127,159,231,252,247,254,0,255,143,240,0,255
,31,252,7,248,127,159,239,254,247,255,1,255,15,240,0,255
,31,254,15,248,127,191,255,255,247,255,131,255,15,240,1,255
,15,255,31,240,127,63,252,255,227,255,199,254,15,224,1,254
,15,255,159,240,255,63,248,255,227,255,231,254,31,224,1,254
,7,255,223,224,255,127,224,127,225,255,247,252,31,224,3,254
,1,255,223,225,254,255,128,127,192,127,247,252,63,192,7,252
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










// EEPROM addresses for persisted data
const int CompassXOffsetAddress = 0;
const int CompassYOffsetAddress = 8;
const int CompassZOffsetAddress = 16;

//This is the enable pin for the IrDa Serial Port
const int IrDaEnablePin = 5;
//This is the Rx/Tx pins for the IrDa Serial Port
#define RxIR A0
#define TxIR A1

//Piezo Speaker Pin
const int speakerPin = 4;

//Battery voltage divider
const int vRegMonPin = A2;




//Create the PWM Servo driver object
Adafruit_PWMServoDriver pwm = Adafruit_PWMServoDriver(0x78);

DigoleSerialDisp mydisp(&Wire,'\x27');

//Create the SoftSerial interface object
SoftwareSerial infraredSerial(RxIR, TxIR);

//This is what is required for the timer event support
Timer tmr;





//SoftSerial Support Variables
int intPipeCnt = 0;
String aryInput[4];
String temp;
const unsigned int MAX_INPUT = 50;






// Depending on your servo make, the pulse width min and max may vary, you 
// want these to be as small/large as possible without hitting the hard stop
// for max range. You'll have to tweak them as necessary to match the servos you
// have!
//#define SERVOMIN  120 // this is the 'minimum' pulse length count (out of 4096)
//#define SERVOMAX  460 // this is the 'maximum' pulse length count (out of 4096)
#define SERVOMIN  140 // this is the 'minimum' pulse length count (out of 4096)
#define SERVOMAX  430 // this is the 'maximum' pulse length count (out of 4096)
double ServoOffset;  //Find the zero center of the servo offset.  We want the positional output to reflect turning...
//
//
//Trying these settings with the Motor Controller
const uint16_t MOTORZERO = 0; // this is the 'minimum' pulse length count (out of 4096)
const uint16_t MOTORREADY = 200; // this is the 'minimum' pulse length count (out of 4096)
const uint16_t MOTORSTART = 230; // was 275...  this is the 'minimum' pulse length count (out of 4096)
//const uint16_t MOTORSTART = 292; // was 275...  this is the 'minimum' pulse length count (out of 4096)
//const uint16_t MOTORIDLE = 302; // this is the 'minimum' pulse length count (out of 4096)
//const uint16_t MOTORIDLE = 310; // this is the 'minimum' pulse length count (out of 4096)
const uint16_t MOTORIDLE = 250; // this is the 'minimum' pulse length count (out of 4096)
//const uint16_t MOTORMAX = 320; // 250this is the 'maximum' pulse length count (out of 4096)
const uint16_t MOTORMAX = 260; // 250this is the 'maximum' pulse length count (out of 4096)
// our servo # counter
uint8_t servochannelnum = 1;
uint16_t LastMOTOR;
double targHeading = 90;
int8_t valDirection = 0;
int8_t dwellCount = 0;
int8_t dwlTotalCount = 0;
int8_t dwellTest = 3; // this is minimum number of times the maneuver test must pass before a position is considered "hit"
float heading=0;
float turnRate=0;
boolean valDirection2 = false;
boolean dirPassN = false;
boolean dirPassS = false;
boolean dirPassE = false;
boolean dirPassW = false;
double baseFoundHeading = -1;   //This is the base station heading value...  -1 is the unassigned default
const double searchHeadingIncrement = 30; // This is how much we will increment the search angle every XX seconds
const uint16_t maxListensBeforeHeadingChange = 700; // 1/10th of a second for each maneuver... 1 second for each increment
int8_t listenCount = 0;
double findTargetHeading = 0;   //This is the base station heading value...  -1 is the unassigned default
boolean findTarget = false;


boolean MotorRunning = false;
boolean cmgActive = false;
boolean CMGTestState = false;
boolean servoTestState = false;
int motorspeed = 0;    // variable to store the servo position 
const int motorinit = 165;    // variable to store the servo position 
const int motorlow = 200;    // variable to store the servo position
int pos = 0;    // variable to store the servo position 
int posLast = 315;    // variable to store the servo position 
int posCenter = 315;    // variable to store the servo position 
//int posLeft = 450;    //  variable to store the servo position 
//int posRight = 120;    // variable to store the servo position 
int posLeft = 460;    // variable to store the servo position 
int posRight = 170;    // variable to store the servo position 
int posDelay = 10;





//Cosmoneer PID settings
//#define propGAIN  .1 // .1 proportional gain (the bigger the number the harder the controller pushes)
#define propGAIN  .04 // .1 proportional gain (the bigger the number the harder the controller pushes)
//#define intGAIN  .07 // .05 integral gain  (the SMALLER the number (except for 0, which turns it off,)  the more quickly the controller reacts to load changes, but the greater the risk of oscillations.)
#define intGAIN  .2 // .05 integral gain  (the SMALLER the number (except for 0, which turns it off,)  the more quickly the controller reacts to load changes, but the greater the risk of oscillations.)
float intgError;
float lastError;
float dervError;
//#define dervGAIN  3 // .5 derivative gain  (the bigger the number  the more the controller dampens oscillations (to the point where performance can be hindered))
#define dervGAIN  20 // .5 derivative gain  (the bigger the number the more the controller dampens oscillations (to the point where performance can be hindered))








//OLED Display variables
#define LCDCol 16
#define LCDRow 4
#define LCDW 128
#define LCDMaxDelayCount 4
int LCDDelayCount;









boolean InitPower = false;    //This is the initial Power UP State...  This is zero if we have just powered up!  It will be one after we have powered completely up.
boolean SleepState = false;






/*
byte patterns[18] = {
 B10000000, 100,
 B01000000, 100,
 B00100000, 100,
 B00010000, 100,
 B00001000, 100,
 B00000100, 100,
 B00000010, 100,
 B00000001, 100
 };
 */
int LEDindex = 0;
int LEDState = 0;
int mirIndex = 0;
int patternCount = 0;   //sizeof(patterns) / 2;
int ShowLEDCount = 0;   
int pingpoingPoint = 0;
byte LEDOutput = 0;
byte LEDOutTemp = 0;
byte LEDOutHold = 0;
byte LEDSetup = 0;
byte StoredSetup = 0;
int demoLEDCount = 0;//1 = Cycle LEDs
int DelayCount = 0;




int idxSensorToRead = 0;


int value = 0; // set values you need to zero









void loop() {

  // if serial data available, process it
  //processIncomingIrDa();


  //Run the timer events
  //tmr.update();
  CycleLEDs();
  Maneuver();
}





void setup() {
  //Before we do anything else, let the user know we are doing something!
  bleep(3, 25, 500, 80, 3, false);



  //Prepare the port so we can see debug messages!
  Serial.begin(9600); // opens serial port, sets data rate to 9600 bps







  //initIrDa();

  //Initialize variables as needed
  setVariables();

  //Setup pins, as required
  setPins();


  //Start the I2C interface
  Wire.begin();




  initDisplay();
  intIMU();
  
  i2cScan();
  delay(3000);

  initPWM();
  initESC();
  initCompass();
  
  mydisp.clearScreen(); //Clear screen
  delay(100);
  mydisp.clearScreen(); //Clear screen
  delay(100);
  mydisp.setRot180();
  


  //Set the "I am initialized" flag
  InitPower = true;    //We have completely powered up.  Now set the flag so we know we are already running
  //let the user know we are going into the Main Loop!
  //bleep(byte numBleeps, byte numTones, word bgnFreq, int stpFreq, byte milDelay)
  bleep(1, 20, 3500, -150, 5, false);


  //Set the LED timer event
  //tmr.every(100, CycleLEDs);
  //Set the Compass timer event
  //tmr.every(500, ReadCompass2);
  //Set the Maneuver timer event
  //tmr.every(1500, Maneuver);
  //Set the Sensor timer event
  //tmr.every(1000, readSensors);
  //
  //tmr.every(100, Maneuver);


}

void intIMU(){
    mpu.initialize();

    
    //Setup the IMU for I2C pass-through
    mpu.setIntI2CMasterEnabled(false);
    mpu.setI2CBypassEnabled(true);
    mpu.setSleepEnabled(false);
    //i2c_writeReg(0x68, 0x37, 0x02);
    Serial.println(F("Passthrough setup compelte"));

    Serial.println(F("Testing device connections..."));
    Serial.println(mpu.testConnection() ? F("MPU6050 connection successful") : F("MPU6050 connection failed"));
}

void initIrDa(){
  //Turn on the IrDa Transcoder
  pinMode(IrDaEnablePin, OUTPUT);
  digitalWrite(IrDaEnablePin, LOW);  //LOW is off, HIGH is on!
  //delay(1000);  
  //digitalWrite(IrDaEnablePin, HIGH);  //LOW is off, HIGH is on!
  //delay(5000);
  //infraredSerial.begin(9600);
}

void initDisplay(){
  mydisp.begin();
  delay(500);
  /*----------for text LCD adapter and graphic LCD adapter ------------*/
  mydisp.clearScreen(); //Clear screen
  delay(100);
  mydisp.clearScreen(); //Clear screen
  delay(100);
  mydisp.displayConfig(0);
  delay(100);
  mydisp.displayConfig(0);
  delay(100);
  mydisp.undoRotation();
  delay(100); 
  mydisp.displayStartScreen(0);
  delay(100);

  mydisp.drawBitmap(0,0,128,64,startscreenIV);
  delay(3000);

  //mydisp.setLCDColRow(16,7);  //This doesn't work for the 0.96" OLED Display!
  //mydisp.clearScreen(); //Clear screen
  delay(500);
  //mydisp.clearScreen(); //Clear screen
  //delay(100);
  mydisp.disableCursor(); //disable cursor, enable cursore use: enableCursor();
  //mydisp.undoRotation();
  mydisp.setRot180();
}

void initPWM(){
  initstatusbar();
  mydisp.print("Init PWM");
  Serial.println("Init PWM");
  pwm.reset();
  pwm.begin();
  pwm.setPWMFreq(50);  // 60 is the maximum PWM frequency for Servos, suggest using 50 instead

  delay(500);
  //center the servo...
  //warning, this won't be graceful if the servo
  //is somewhere else
  pwm.setPWM(1, 0, posCenter);
  delay(500);
  //zero the servo...
  pwm.setPWM(1, 0, 0);

}

void initCompass(){
  initstatusbar();
  mydisp.print("Init Compass");
  Serial.println("Init Compass");
  LoadParameters();  //Load parameters from EEProm
  //compass_x_offset = -413.98;
  //compass_y_offset = 549.80;
  //compass_z_offset = 83.99;
  compass_init(2);

  //timerDelay(1000);
  delay(1000);


  initstatusbar();
  mydisp.print("Init Compass Tst");
  //
  CompassCalibrationCheck();
  //
  initstatusbar();
  mydisp.print("Test Complete");
}

void initESC(){
  //zero the servo...
  pwm.setPWM(1, 0, 0);

  
  initstatusbar();
  mydisp.print("Init ESC");
  //Use this sequence to reset the Min/Max settings on the Mx-3A ESC!!
  pwm.setPWM(0, 0, MOTORZERO);  //Set the PWM to 0%, instructing the ESC that we are at the ZERO position
  delay(7000);  //These timings are critical here...  Wait seven seconds
  pwm.setPWM(0, 0, MOTORMAX);   //Set the PWM to 100%
  delay(1000);  //These timings are critical here...
  pwm.setPWM(0, 0, MOTORSTART);
  delay(1000);  //These timings are critical here...
  pwm.setPWM(0, 0, MOTORREADY);
  delay(7000);  //These timings are critical here...
}





boolean GetCheckSum(){
  byte chkSum = 0;

  for (int i = 0; i < 4;i++){
    temp = aryInput[i];
    for (int j = 0; j < temp.length();j++){
      chkSum += byte(temp[j]);
    }
    chkSum += byte('|');
  }
  if (chkSum == byte('\n')){
    chkSum +=1;
  }
  if (String(chkSum) == aryInput[4]) {
    return true;
  }
  else
  {
    return false;
  }
}



void processIncomingIrDa(){
   String content = "";
   char character;

  //digitalWrite(13, HIGH);

  // if serial data available, process it
  while(infraredSerial.available() > 0) {
      character = infraredSerial.read();
      content.concat(character);
  }

  if (content != "") {
    //mydisp.clearScreen(); //Clear screen
    //initstatusbar();
    //mydisp.print(content); 
    //LEDSetup = B00110111;
    //ShowLEDCount = 5;
    //delay(50);
    
    char content2[content.length()];
    content.toCharArray(content2, content.length());
    char *i;
    char* command = strtok_r(content2, "|",&i);

    //initstatusbar();
    //mydisp.print(command); 
    //delay(2000);

    if (command == "T") {
      LEDSetup = B00110111;
      ShowLEDCount = 5;
      delay(50);
      command = strtok_r(NULL,":",&i);
      command = strtok_r(NULL,":",&i);
      initstatusbar();
      mydisp.print(command); 
      //delay(2000);
      findTargetHeading = atof(command);
      findTarget = true;
    }
    else
    {
      if (content == "?|01|NA") {
        baseFoundHeading = targHeading;
      }
    }

  }
  else
  {
    //mydisp.clearScreen(); //Clear screen
    //mydisp.drawStr(0, 0, "No Data"); //display string at: x=0, y=0
    //delay(100);
    //LEDSetup = B00110111;
    //LEDOutput = B10011001;
    //ShowLEDCount = 2;
  }

  //digitalWrite(13, LOW);
}  








void initstatusbar()
{
  mydisp.setTextPosAbs(0,59);
  mydisp.print("                ");
  mydisp.setTextPosAbs(0,59);
}





//----------------------------------------------------------------
//
//
//   This section contains Setup subroutines
//
//
//----------------------------------------------------------------
void setVariables() {
  uint32_t currentFrequency;
}

void setPins() {
  analogReference(INTERNAL);

  //This pin is used for system activity feedback to the user
  pinMode(13, OUTPUT);
  digitalWrite(13, LOW);



  //byte LEDSetup = 0;
  //1   = On/Off
  //2   = Pattern/All
  //4   = Single/Alternates
  //8   = PingPong/Forward
  //16  = Mirror/Entire
  //32  = Flip Direction
  //64  = Blink/Normal
  //128 = Invert/Normal
  LEDSetup = B00000001;
  LEDOutput = B00000000;  //All Off!
  setLEDArray(LSBFIRST, LEDOutput);
  LEDSetup = B00000001;





  //Just a small delay
  delay(100);
}






void CompassCalibrationCheck() {
  //This subroutine starts the motor
  //and checks to see if a turn will yield
  //all four compass point crossings
  double calLastHeading;
  double calHeadingDiff;
  uint16_t countRevolution = 0;


  Serial.println("Verify Compass Calibration:\t");
  digitalWrite(13, HIGH);

  //read the initial heading
  ReadCompass2();
  //set the last heading value
  calLastHeading = bearing;

  //start the motor
  runMotor(MOTORMAX);
  //run the motor up to speed
  runMotor(MOTORMAX);

  //runMotor(MOTORSTART);
  //delay(3000);
  //runMotor(MOTORMAX);
  //slight delay
  delay(300);
  //turn towards the right, or a clockwise spin
  setServo(240);
  //posCenter = 340 
  //int posLeft = 530 
  //int posRight = 120 
  //slight delay
  delay(300); 



  //initstatusbar();
  //mydisp.print("Testing");
  //delay(1000); 
  for(uint16_t steps = 0; steps<10; steps++)     // steps goes from 0 to 10 
  {                                
    Serial.println("Sre:\t");
    for(uint16_t calsteps = 0; calsteps<10; calsteps++)     // calsteps goes from 0 to 10 
    {                                
      // waits 100ms before reading the next position
      digitalWrite(13, LOW);
      delay(100); 
      digitalWrite(13, HIGH);
      //read the current heading
      ReadCompass2();

      //Calculate the difference
      calHeadingDiff = bearing - calLastHeading;

      initstatusbar();
      mydisp.print("Testing: ");
      mydisp.print((int) round(calLastHeading)); //display string at: x=0, y=0
      mydisp.print("/"); //display string at: x=0, y=0
      mydisp.print((int) round(bearing)); //display string at: x=0, y=0

      if (calLastHeading < 90 && bearing > 90 && dirPassE == false) {
        dirPassE = true;
        bleep(1, 2, 3500, -500, 5, false);
      }
      if (calLastHeading < 180 && bearing > 180 && dirPassS == false) {
        dirPassS = true;
        bleep(1, 3, 3500, -500, 5, false);
      }
      if (calLastHeading < 270 && bearing > 270 && dirPassW == false) {
        dirPassW = true;
        bleep(1, 4, 3500, -500, 5, false);
      }
      if (calLastHeading < 360 && bearing > 0 && dirPassN == false) {
        dirPassN = true;
        bleep(1, 1, 3500, -500, 5, false);
      }
      if (dirPassE && dirPassS && dirPassW && dirPassN) {
        dirPassE = false;
        dirPassS = false;
        dirPassW = false;
        dirPassN = false;
        countRevolution +=1;
        mydisp.print(".");
        //bleep(byte numBleeps, byte numTones, word bgnFreq, int stpFreq, byte milDelay)
        bleep(4, 20, 1000, 50, 1, false);
      }
      calLastHeading = bearing;
    } 
    //bleep(byte numBleeps, byte numTones, word bgnFreq, int stpFreq, byte milDelay)
    //bleep(1, 20, 3500, -150, 10);
    bleep(1, 10, 3500, -300, 3, false);
  } 
  digitalWrite(13, LOW);


  if (countRevolution > 0) {
    bleep(3, 25, 500, 80, 3, false);
  }
  else
  {
    //calibration is needed!!
    bleep(1, 2, 3500, -2000, 10, false);
    setServo2(posCenter);
    delay(500);
    //pwm.setPWM(1, 0, 240);
    setServo2(220);
    initstatusbar();
    mydisp.print("Calibrating!");
    compass_debug = 1;
    //compass_offset_calibration(3);
    compass_offset_calibration(2);
    SaveParameters();    //Save parameters after the calibration
  }
  dirPassE = false;
  dirPassS = false;
  dirPassW = false;
  dirPassN = false;

}















//----------------------------------------------------------------
//
//
//   This section contains the Contol Moment Gyro subroutines
//
//
//----------------------------------------------------------------
void Maneuver() {
  //This Sub calls the main sub, passing the appropriate values
  if (cmgActive == false) {
    cmgActive = true;



/*
    if (baseFoundHeading == -1) {
      listenCount +=1;
      if (listenCount > maxListensBeforeHeadingChange) {
        targHeading += searchHeadingIncrement;
        if (targHeading >= 360) {
          targHeading = 0;
        }
        listenCount =0;
      }
    }
    else
    {
      if (findTarget == true) {
        targHeading = findTargetHeading;
      }
      else
      {
        targHeading = baseFoundHeading;
      }
    }
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

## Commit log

2014-06-28 Initial Commit
    This is the initial Comoneer Junior design. Expect some changes in the
    future. Will publish the source code in a separate repository.
    [CosmoneerJr.kicad_pcb, CosmoneerJr.sch]
2014-07-01 PDF added
    Generated a pdf version of the schematic
    Schematic fixes made
    Net connections on U1 were disconnected during component move. Nets
    reconnected, pdf generated, netlist generated and re-imported into pcb.
    PCB file updated and saved.
    [CosmoneerJr.kicad_pcb, CosmoneerJr.sch]
2014-11-14 Pressfit PCB additions
    Added pads, drills and Silkscreen outlines for press fit pcb additions.
    [CosmoneerJr.kicad_pcb, CosmoneerJr.sch]
2015-01-01 Moved parts and run lines
    Moved several parts and began running traces. Added two additional
    internal layers, bringing the board to a total of four layers.
    [CosmoneerJr.kicad_pcb]
2015-02-12 new changes
    More routing and parts movement
    [CosmoneerJr.kicad_pcb]
2015-02-13 Final changes
    [CosmoneerJr.kicad_pcb, CosmoneerJr.sch]
2015-02-15 Final changes
    Re-added mounting holes and migrated pressFit silk screen to back side
    of PCB
    [CosmoneerJr.kicad_pcb]
2015-02-17 Rev Zero Prototype
    Silkscreen cleanup, minor part movements
    [CosmoneerJr.kicad_pcb]
2015-02-17 Generated PCB Fabrication Files
    Generated and edited pcb files. Made a couple of minor cleanup fixes to
    inner copper layer 2.
    [CosmoneerJr-Edge_Cuts.gbr, CosmoneerJr-L1.gbr, CosmoneerJr-L1_Mask.gbr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]
2015-02-19 Rev Zero Cleanup
    Eliminated vias and extra verticies in traces. Prepared bottom
    silkscreen to merge with bottom layer.
    [CosmoneerJr-Edge_Cuts.gbr, CosmoneerJr-L1.gbr, CosmoneerJr-L1_Mask.gbr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]
2015-07-26 Rev ZeroOne Prototype
    Parts added, Schematic updated and PCB updated and Mfg files generated
    [CosmoneerJr-Edge_Cuts.gbr, CosmoneerJr-L1.gbr, CosmoneerJr-L1_Mask.gbr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]
2015-09-19 Rev 02
    Fixes made to PCB for Rev 02. Additional files for Rev 01/02 design
    added to repository.
    [BalancerFeet.stl, BalancerMain.stl, ChargeCover_v4.stl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]
2015-11-17 Compass Self-Cal
    Compass self calibration code implemented. Lower speed setup for ESC &
    gyro motor. Compass point headings are now sought out by the Cosmoneer.
    End user may need to comment out the current sensor code (INA219 library
    reference).
2016-09-30 IrDa and SuperBurst Additions
    Additions and changes to projects
    [IrDA-B.Cu.gbr, IrDA-B.Mask.gbr, IrDA-B.SilkS.gbr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]
2017-06-26 OLED & Compass Updates
    Removed timers in favor of constant maneuverung calls via main loop.
    Compass smoothing function was reworked. OLED display updates and
    library updates made. Changes made to support Arduino interface version
    1.6.10.
    [Evolution_18_2_MX_3A_STEM.ino]
2017-07-17 PID Loop timing changes
    Changes made to the PID loop to remove "delay" programming. Counters
    introduced to trigger events after so many loops, as the refresh rate
    was too high for some events and the devices attempting to be refreshed.
    [Evolution_18_2_MX_3A_STEM.ino]
2018-02-23 Evo 18.5 Upload
    Reverted back to 16.8 target selection code and 16.8 setServo subroutine
    usage. Fixed logo display issue on startup, as well as moved and
    modified the servo centering step, so it centered the servo and then
    released the servo. This resulted in a reduction of current draw by the
    servo during motor startup. Once started, the servo could be re-engaged
    from the "center" position. This code also uses the GY-86 board, which
    requires the MPU-6050 to be set to I2C Passthrough, in order to directly
    communicate with the compass.
    A physical change to the PCB was to remove and bypass the 300mA
    resettable fuse and remove the protection diode.
    [Evolution_18_5_MX_3A_STEM.ino]
